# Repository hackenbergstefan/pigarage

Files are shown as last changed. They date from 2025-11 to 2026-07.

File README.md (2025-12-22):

# PiGarage - Smartify your garage gate with license plate recognition

PiGarage controls a gate using a camera, IR sensors, and MQTT. It detects motion, finds license plates, performs OCR, and triggers gate actions based on allowed plates and motion direction.

- [PiGarage - Smartify your garage gate with license plate recognition](#pigarage---smartify-your-garage-gate-with-license-plate-recognition)
  - [Hardware Setup](#hardware-setup)
  - [Software component interaction](#software-component-interaction)
    - [Components](#components)
    - [OcrDetector Preprocessing Steps](#ocrdetector-preprocessing-steps)
  - [Example of image processing pipeline](#example-of-image-processing-pipeline)
  - [Raspberry Pi Shield](#raspberry-pi-shield)
  - [Housing](#housing)

## Hardware Setup

```
___________________________________________________
||          🚥          📷          🔦          ||
||     [Status LED]   [Camera]    [IR Beam]      ||
||                                               ||
||                      📟                       ||
||                 [Raspberry Pi]                ||
||                                         ⛓️    ||
||                                       [Motor] ||
||                                               ||
||                                               ||
||🚧                                          🚧||
||[IR Barrier]                       [IR Barrier]||
||_______________________________________________||
```

Legend:
- 📷 Camera and 🔦 IR Beam mounted at top center above the gate opening.
- 🚧 IR Barrier sensors placed low on left and right sides near the ground.
- 📟 Raspberry Pi
- ⛓️ Motor controlling the gate
- 🚥 Status LED indicating system state

I'm using the following hardware components:
- 📟 Raspberry Pi 4 Model B
- 📷 [IR Camera module](https://www.az-delivery.de/products/raspberry-pi-kamera-nachtsicht-infrarot-kameramodul-5mp-ov5647-webcam)
- 🔦 [IR illuminator](https://www.amazon.de/dp/B09H74YTHN)
- 🚧 [IR Barrier sensors](https://www.amazon.de/dp/B0DY465JHQ)
- 🚥 [Neopixel Ring 12x](https://www.adafruit.com/product/2853)

## Software component interaction

This section illustrates how `LicensePlateProcessor` coordinates the threads `DifferenceDetector`, `PlateDetector`, and `OcrDetector`, including their queue-based communication and pause/resume lifecycle.

```mermaid
sequenceDiagram
    participant LP as LicensePlateProcessor
    participant DD as DifferenceDetector
    participant PD as PlateDetector
    participant OD as OcrDetector

    LP->>DD: resume()
    activate DD
    Note over LP: wait<br> for diff
    DD-->>LP: notify()
    LP->>DD: pause()
    deactivate DD

    LP->>PD: resume()
    activate PD
    Note over PD: Detect plate with YOLO<br/>enqueue plate crop<br/>infer motion direction

    LP->>OD: resume()
    activate OD
    Note over OD: wait()<br> for plate
    OD->>PD: get plate
    Note over OD: Consume plate crop<br/>OCR with EasyOCR

    Note over LP: wait<br> for allowed plate
    OD-->>LP: notify(allowed_plate)
    OD->>OD: pause()
    deactivate OD

    Note over LP: wait<br> for direction
    PD-->>LP: notify(direction)
    PD->>PD: pause()
    deactivate PD

    Note over LP: open/close gate<br>send mqtt message
```

### Components

- **DifferenceDetector**: Captures low-resolution frames, computes MSE, notifies on motion, then pauses.
- **PlateDetector**: Uses YOLO to detect plate crops and infers motion direction from vertical history; publishes to `detected_plates` and `detected_directions`.
- **OcrDetector**: Consumes plate crops, preprocesses and OCRs text; if text matches `allowed_plates`, publishes to `detected_ocrs` and pauses.
- **LicensePlateProcessor**: Orchestrates pause/resume, waits for motion, then concurrently runs plate and OCR; reads `detected_ocrs` and `detected_directions` with timeouts, triggers callbacks.

### OcrDetector Preprocessing Steps

In order to improve OCR accuracy, non-plate areas are masked to focus on text and reduce to black and white.
(See [./src/pi_garage/ocr_detector.py::cv2_mask_non_plate](./src/pi_garage/ocr_detector.py))

## Example of image processing pipeline

1. Original image from camera (from huggingface model page):
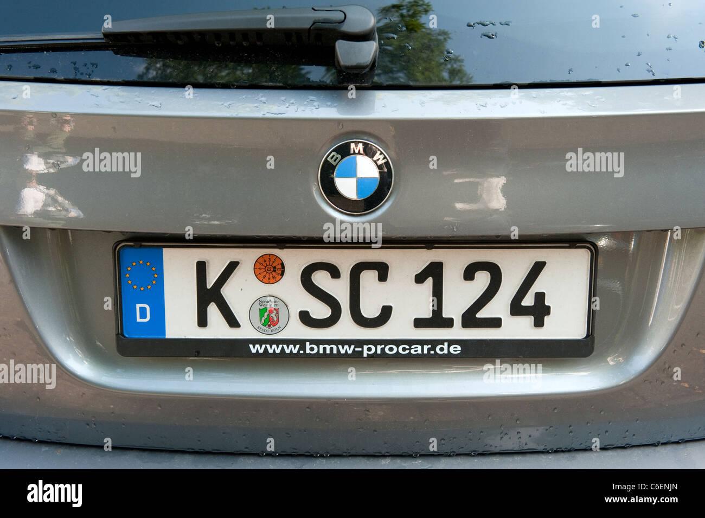
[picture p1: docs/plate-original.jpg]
Original Image
   

2. Detected license plate region (`pigarage-plate-detector ./docs/plate-original.jpg --output ./docs/plate-crop.jpg`):
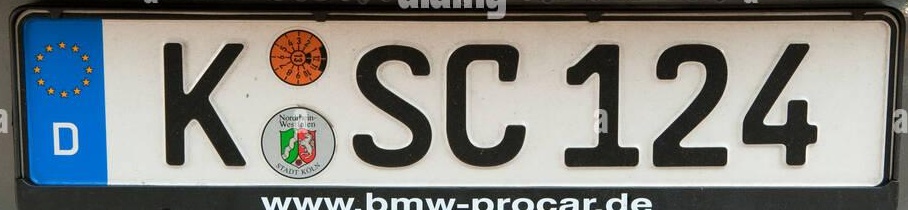
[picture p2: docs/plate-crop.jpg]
Detected Plate
   

3. Masked non-plate areas (`pigarage-ocr-detector improve ./docs/plate-crop.jpg --output ./docs/plate-masked.jpg`):
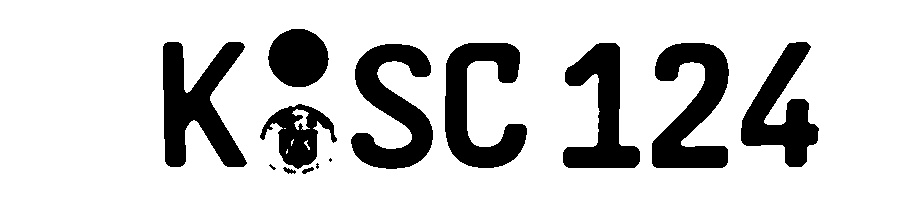
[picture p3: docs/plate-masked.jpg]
Masked Plate
   

4. EasyOCR Result (`pigarage-ocr-detector ocr ./docs/plate-masked.jpg`):
   ```
   K SC 124
   ```

## Raspberry Pi Shield

Wiring diagram for connecting the components to the Raspberry Pi using a custom shield:

Wiring Diagram

See [docs/garage.fzz](docs/garage.fzz) for the Fritzing source file.

## Housing

I designed a custom housing for the camera and the LED ring using Fusion 360.
The source files can be found under [docs/garage-housing.f3d](docs/garage-housing.f3d).
Here are some pictures of the housing:

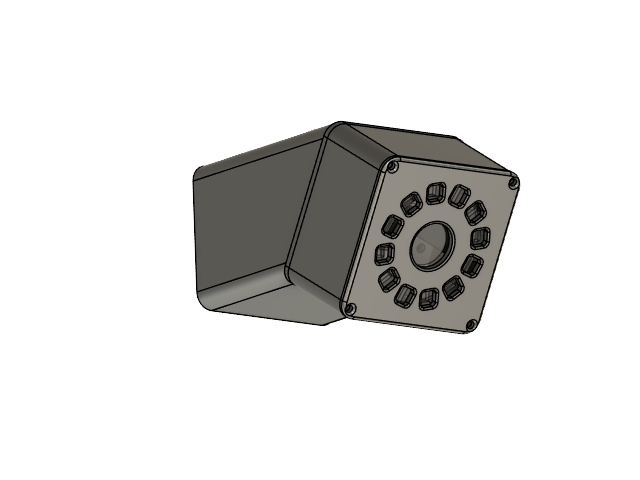
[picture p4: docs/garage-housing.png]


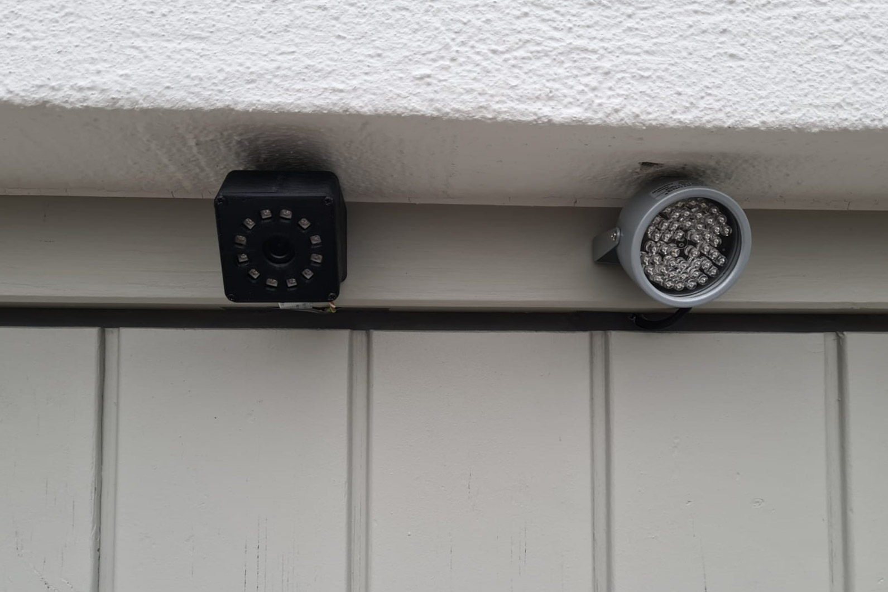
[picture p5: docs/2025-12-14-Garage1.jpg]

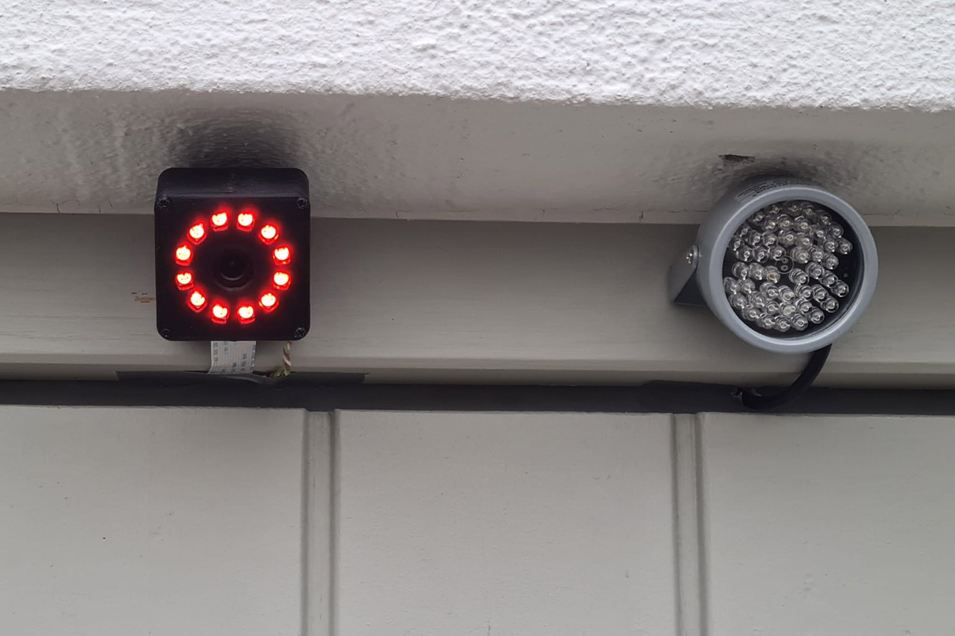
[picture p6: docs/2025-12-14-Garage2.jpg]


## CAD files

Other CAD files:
docs/garage-housing.f3d

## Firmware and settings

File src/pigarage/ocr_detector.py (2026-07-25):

import argparse
import logging
import os
import re
import time
from collections.abc import Callable
from http import HTTPStatus
from http.client import HTTPException
from pathlib import Path
from queue import Queue

os.environ["PADDLE_PDX_ENABLE_MKLDNN_BYDEFAULT"] = "0"

import cv2
import numpy as np
import requests
from paddleocr import PaddleOCR

from .config import VISUAL_DEBUG
from .config import config as pigarage_config
from .util import PausableNotifingThread

TRACE = 5
"""Custom logging level for trace messages."""
logging.addLevelName(TRACE, "TRACE")


def create_ocr() -> PaddleOCR:
    return PaddleOCR(
        lang="en",
        use_doc_orientation_classify=False,
        use_doc_unwarping=False,
        use_textline_orientation=False,
        device="cpu",
        text_rec_score_thresh=0.3,
    )


def cv2_contours_append_children(
    hierarachy: np.ndarray,
    idx: int,
    idxs: set[int],
) -> None:
    if (child := hierarachy[0][idx][2]) != -1:
        idxs.add(child)
        cv2_contours_append_children(hierarachy, child, idxs)
    if (sibling := hierarachy[0][idx][0]) != -1:
        idxs.add(sibling)
        cv2_contours_append_children(hierarachy, sibling, idxs)


def cv2_improve_plate_img(  # noqa: PLR0913
    plate: cv2.typing.MatLike,
    blur: int = 3,
    block_size: int = 181,
    c: float = 2,
    clahe_clip: float = 2.0,
    clahe_tile: int = 5,
    min_plate_area: float = 0.3,
    min_char_height_ratio: float = 0.5,
) -> cv2.typing.MatLike | None:
    plate = cv2.cvtColor(plate, cv2.COLOR_BGR2GRAY) if len(plate.shape) == 3 else plate  # noqa: PLR2004
    plate = cv2.createCLAHE(
        clipLimit=clahe_clip,
        tileGridSize=(clahe_tile, clahe_tile),
    ).apply(plate)
    plate = cv2.resize(plate, None, fx=3, fy=3, interpolation=cv2.INTER_LANCZOS4)

    kernel = np.array([[0, -1, 0], [-1, 5, -1], [0, -1, 0]])
    plate = cv2.filter2D(plate, -1, kernel)

    thresh = cv2.adaptiveThreshold(
        src=cv2.medianBlur(plate, blur),
        maxValue=255,
        adaptiveMethod=cv2.ADAPTIVE_THRESH_GAUSSIAN_C,
        thresholdType=cv2.THRESH_BINARY,
        blockSize=block_size,
        C=c,
    )

    # Calculate contours
    contours, hierarachy = cv2.findContours(
        thresh, cv2.RETR_TREE, cv2.CHAIN_APPROX_SIMPLE
    )
    # Calculate areas of contours and sort them descending
    areas = np.array([cv2.contourArea(c) for c in contours])
    if np.all(areas == 0):
        logging.getLogger(__name__).log(TRACE, "All contours have zero area")
        return None
    idxs = np.argsort(areas)[::-1]
    # Check that plate area is large enough
    if areas[idxs[0]] / (plate.shape[0] * plate.shape[1]) < min_plate_area:
        logging.getLogger(__name__).log(
            TRACE,
            "Plate area too small: %.2e",
            areas[idxs[0]] / (plate.shape[0] * plate.shape[1]),
        )
        return None

    heights = np.array([cv2.boundingRect(c)[3] for c in contours], dtype=np.float32)
    heights /= heights[idxs[0]]

    idxs_to_draw = {i for i in idxs[1:] if heights[i] > min_char_height_ratio}
    if hierarachy.shape[1] > 1000:  # noqa: PLR2004
        logging.getLogger(__name__).log(
            TRACE,
            f"Too many contours ({len(hierarachy)}), skipping child contours",
        )
        return None
    for i in idxs_to_draw.copy():
        cv2_contours_append_children(hierarachy, i, idxs_to_draw)

    masked = cv2.drawContours(
        cv2.bitwise_not(np.zeros(thresh.shape).astype(thresh.dtype)),
        [contours[i] for i in idxs_to_draw],
        -1,
        color=(0, 0, 0),
        thickness=cv2.FILLED,
    )
    # Remove everything outside the largest contour (the plate)
    plate_background = cv2.drawContours(
        np.zeros(thresh.shape).astype(thresh.dtype),
        [contours[idxs[0]]],
        -1,
        color=(255, 255, 255),
        thickness=cv2.FILLED,
    )
    masked = cv2.bitwise_or(masked, cv2.bitwise_not(plate_background))
    if VISUAL_DEBUG:
        cv2.imshow("masked", masked)
        cv2.waitKey(0)
        cv2.destroyAllWindows()
    return masked


def plate2text(plate: cv2.typing.MatLike, ocr: PaddleOCR | None = None) -> str:
    ocr = ocr or create_ocr()
    result = ocr.predict(plate)[0]
    logging.getLogger(__name__).debug(
        f"OCR result: {result['rec_texts']} with {result['rec_scores']}"
    )
    return result["rec_texts"][0]


class OcrDetector(PausableNotifingThread):
    def __init__(  # noqa: PLR0913
        self,
        detected_plates: Queue,
        allowed_plates: list[str],
        ocr_regex: str = r"[A-Z]{1,2}\.? ?\.?[A-Z]{0,2} ?[0-9]{2,4}$",
        on_ocr_detected: Callable[[str], None] = lambda _: None,
        *,
        cv2_improve_plate_img_kwargs: dict | None = None,
        debug: bool = False,
    ) -> None:
        super().__init__()
        self._debug = debug
        self._detected_plates = detected_plates
        self.detected_ocrs = Queue(maxsize=1)
        self._ocr_regex = ocr_regex
        self._ocr = create_ocr()
        self.allowed_plates = allowed_plates
        self._on_ocr_detected = on_ocr_detected
        self._remote_session = requests.Session()
        self._cv2_improve_plate_img_kwargs = cv2_improve_plate_img_kwargs

    def resume(self) -> None:
        while self.detected_ocrs.qsize() > 0:
            self.detected_ocrs.get_nowait()
        return super().resume()

    def _postprocess(self, ocr: str) -> str:
        ocr = re.search(self._ocr_regex, ocr)
        if ocr:
            return ocr.group(0)
        return None

    def _process_remote(self, plate: cv2.typing.MatLike) -> str | None:
        logging.getLogger(__name__).debug("Using remote OCR")
        plate = cv2.cvtColor(plate, cv2.COLOR_BGR2GRAY)
        response = self._remote_session.post(
            f"{pigarage_config.client['url']}/ocr",
            headers={"auth": pigarage_config.client["auth"]},
            data=cv2.imencode(".jpg", plate)[1].tobytes(),
        )
        if response.status_code != HTTPStatus.OK:
            raise HTTPException(f"Remote OCR failed with {response.status_code}")
        return response.json().get("result")

    def _process_local(self, plate: cv2.typing.MatLike) -> str | None:
        logging.getLogger(__name__).debug("Using local OCR")
        plate = cv2_improve_plate_img(
            plate, **(self._cv2_improve_plate_img_kwargs or {})
        )
        if plate is None:
            return None
        if self._debug:
            cv2.imwrite(
                pigarage_config.logdir
                / f"{time.strftime('%Y-%m-%d_%H-%M-%S')}_ocr_post.jpg",
                plate,
            )
        return plate2text(plate, ocr=self._ocr)

    def process(self) -> None:
        plate = self._detected_plates.get()

        if self._debug:
            cv2.imwrite(
                pigarage_config.logdir
                / f"{time.strftime('%Y-%m-%d_%H-%M-%S')}_ocr_pre.jpg",
                plate,
            )

        if "url" in pigarage_config.client:
            try:
                result = self._process_remote(plate)
            except (requests.RequestException, HTTPException) as e:
                logging.getLogger(__name__).warning(
                    f"Remote OCR failed, falling back to local OCR: {e}"
                )
                result = self._process_local(plate)
        else:
            result = self._process_local(plate)

        ocr = self._postprocess(result)
        self._log.info(f"OCR: '{result.strip()}' -> '{ocr}'")
        if ocr is not None:
            self._on_ocr_detected(ocr)
        if ocr is not None and ocr in self.allowed_plates:
            self.detected_ocrs.put(ocr)
            self._notify_waiters()
            self.pause()


def main() -> None:
    logging.basicConfig(level=TRACE)
    parser = argparse.ArgumentParser()
    parser.add_argument(
        "action",
        choices=("improve", "ocr"),
        help="Action to perform",
    )
    parser.add_argument("input", type=Path, help="Path to the image file")
    parser.add_argument(
        "--output",
        type=Path,
        help="Path to save the output image. "
        "If not provided, the image will be shown using cv2.imshow.",
    )
    parser.add_argument(
        "--visual-debug",
        action="store_true",
        help="Enable visual debug mode with additional output.",
    )
    args = parser.parse_args()

    global VISUAL_DEBUG  # noqa: PLW0603
    VISUAL_DEBUG = args.visual_debug
    img = cv2.imread(str(args.input))

    match args.action:
        case "improve":
            out = cv2_improve_plate_img(img)
        case "ocr":
            result = plate2text(img)
            logging.getLogger(__name__).info(f"OCR result: '{result}'")
            return

    if args.output:
        cv2.imwrite(str(args.output), out)
    else:
        cv2.imshow("output", out)
        cv2.waitKey(0)
        cv2.destroyAllWindows()


if __name__ == "__main__":
    main()

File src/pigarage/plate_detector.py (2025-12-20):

import argparse
import logging
import time
from collections.abc import Callable
from dataclasses import dataclass
from pathlib import Path
from queue import Queue

import cv2
import ultralytics
from huggingface_hub import hf_hub_download
from ultralytics import YOLO

try:
    from picamera2 import Picamera2
except ImportError:
    from unittest.mock import MagicMock

    Picamera2 = MagicMock()

from .config import config as pigarage_config
from .util import PausableNotifingThread


def increment_path_exists_ok(
    path: str | Path,
    *,
    exist_ok: bool = False,  # noqa: ARG001
    sep: str = "",  # noqa: ARG001
    mkdir: bool = False,  # noqa: ARG001
) -> Path:
    return path


ultralytics.utils.files.increment_path = increment_path_exists_ok
ultralytics.utils.LOGGER.setLevel(logging.WARNING)


@dataclass
class Box:
    x1: int
    y1: int
    x2: int
    y2: int

    @property
    def center_x(self) -> float:
        return (self.x1 + self.x2) / 2

    @property
    def center_y(self) -> float:
        return (self.y1 + self.y2) / 2


class PlateHistory:
    def __init__(self, different_plate_distance: int) -> None:
        self._boxes: list[Box] = []
        self._different_plate_distance = different_plate_distance

    def get(self, box: Box) -> Box | None:
        """Get existing plate close to center_x, if any."""
        for prev_box in self._boxes:
            if abs(box.center_x - prev_box.center_x) < self._different_plate_distance:
                return prev_box
        return None

    def update_x(self, box: Box) -> None:
        """Update x position of existing plates to account for movement."""
        for prev_box in self._boxes:
            if abs(box.center_x - prev_box.center_x) < self._different_plate_distance:
                prev_box.x1 = box.x1
                prev_box.x2 = box.x2

    def add_or_update(self, box: Box) -> bool:
        """Add new plate position or update existing one."""
        if self.get(box) is not None:
            self.update_x(box)
            return False
        self._boxes.append(box)
        return True

    def clear(self) -> None:
        self._boxes = []


class PlateDetector(PausableNotifingThread):
    def __init__(  # noqa: PLR0913
        self,
        cam: Picamera2,
        cam_setting: str = "main",
        on_resume: Callable[[], None] = lambda: None,
        on_notifying: Callable[[], None] = lambda: None,
        direction_min_distance: int = 50,
        direction_ignore_distance: int = 5,
        different_plate_distance: int = 100,
        *,
        debug: bool = False,
    ) -> None:
        super().__init__(on_resume=on_resume, on_notifying=on_notifying)
        self.model = YOLO(
            hf_hub_download(
                "morsetechlab/yolov11-license-plate-detection",
                "license-plate-finetune-v1n.pt",
            )
        )
        self._cam = cam
        self._cam_setting = cam_setting
        self._debug = debug
        self.detected_plates = Queue(maxsize=0)
        self.detected_directions = Queue(maxsize=0)
        self._direction_min_distance = direction_min_distance
        self._direction_ignore_distance = direction_ignore_distance
        self._different_plate_distance = different_plate_distance
        self._history = PlateHistory(different_plate_distance)

    def resume(self) -> None:
        while self.detected_plates.qsize() > 0:
            self.detected_plates.get_nowait()
        while self.detected_directions.qsize() > 0:
            self.detected_directions.get_nowait()
        self._history.clear()
        return super().resume()

    def _detect_plate_boxes(self, img: cv2.typing.MatLike) -> list[Box]:
        results = self.model.predict(
            source=img,
            verbose=False,
            save=self._debug,
            save_crop=self._debug,
            project="/tmp",  # noqa: S108
            name="plate_detector",
            imgsz=512,
        )
        boxes: list[Box] = []
        # Detect plates
        for box in results[0].boxes:
            x1, y1, x2, y2 = map(int, box.xyxy[0].tolist())
            box = Box(x1, y1, x2, y2)  # noqa: PLW2901
            boxes.append(box)
        return boxes

    def _update_history(self, img: cv2.typing.MatLike, boxes: list[Box]) -> None:
        """Update plate history and notify about new plates."""
        for i, box in enumerate(boxes):
            if self._history.add_or_update(box):
                self._log.debug(
                    f"New plate detected at ({box.center_x}, {box.center_y})"
                )
                if self._debug:
                    cv2.imwrite(
                        pigarage_config.logdir
                        / f"{time.strftime('%Y-%m-%d_%H-%M-%S')}_plate_{i}.jpg",
                        cv2.resize(
                            cv2.rectangle(
                                img,
                                (box.x1, box.y1),
                                (box.x2, box.y2),
                                color=(255, 0, 0),
                                thickness=3,
                            ),
                            dsize=(int(0.2 * img.shape[1]), int(0.2 * img.shape[0])),
                        ),
                    )
                self.detected_plates.put(img[box.y1 : box.y2, box.x1 : box.x2])
                self._notify_waiters()

    def _detect_direction(self, img: cv2.typing.MatLike, boxes: list[Box]) -> None:
        """Detect direction of plates based on y position changes."""
        for box in boxes:
            prev = self._history.get(box)
            if prev is None:
                continue
            if abs(box.center_y - prev.center_y) < self._direction_ignore_distance:
                continue
            self._log.debug(f"Plate updated ({box.center_x}, {box.center_y})")

            self.detected_plates.put(img[box.y1 : box.y2, box.x1 : box.x2])
            self._notify_waiters()

            diff = box.center_y - prev.center_y
            if abs(diff) < self._direction_min_distance:
                return

            direction = "arriving" if diff > 0 else "leaving"
            self._log.debug(f"direction: {direction}")
            self.detected_directions.put(direction)
            self._notify_waiters()

    def process(self) -> None:
        img = self._cam.capture_array(self._cam_setting)
        boxes = self._detect_plate_boxes(img)
        if len(boxes) == 0:
            return
        self._update_history(img, boxes)
        self._detect_direction(img, boxes)
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

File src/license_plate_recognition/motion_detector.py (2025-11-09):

import logging
from typing import Literal

import cv2
import numpy as np
from picamera2 import Picamera2

from .util import DetectionThread


class MotionDetector(DetectionThread):
    def __init__(
        self,
        cam: Picamera2,
        cam_setting="lowres",
        history: int = 50,
        variance_threshold: int = 80,
        resize: int = 480,
        *,
        debug: bool = False,
    ):
        super().__init__(cam=cam, cam_setting=cam_setting)

        self.tracker = cv2.createBackgroundSubtractorMOG2(
            history=history,
            detectShadows=False,
            varThreshold=variance_threshold,
        )
        self.history = []
        self.history_length = 6
        self.resize = resize
        self.debug = debug

    def _center_of_mass(self, img: cv2.typing.MatLike) -> float | None:
        """
        Calculate y-coordinate of center of mass of the convex hull of all contours in the image.
        """
        # Find contours in the image
        contours, _ = cv2.findContours(img, cv2.RETR_EXTERNAL, cv2.CHAIN_APPROX_SIMPLE)
        if not contours:
            return None

        # Calculate the convex hull of the contours
        hull = cv2.convexHull(np.vstack(contours))

        # Calculate the center of mass of the convex hull
        moments = cv2.moments(hull)
        if moments["m00"] == 0:
            return None
        center_x = int(moments["m10"] / moments["m00"])
        center_y = int(moments["m01"] / moments["m00"])

        if self.debug:
            # Draw the convex hull and center of mass on the image for debugging
            img = cv2.cvtColor(img, cv2.COLOR_GRAY2BGR)
            img = cv2.drawContours(img, [hull], -1, color=(255, 0, 0), thickness=3)
            img = cv2.circle(
                img,
                (center_x, center_y),
                radius=7,
                color=(0, 0, 255),
                thickness=-1,
            )
            cv2.imwrite("/tmp/motion_detector.jpg", img)
        return center_y

    def process(self, img: cv2.typing.MatLike) -> None | Literal["arriving", "leaving"]:
        """
        Process the image to detect motion direction based on the center of mass of the convex hull
        of the contours in the foreground mask.
        """
        # img = cv2.resize(
        #     img,
        #     dsize=(self.resize, int(img.shape[0] / img.shape[1] * self.resize)),
        # )
        fg_mask = self.tracker.apply(img)
        center_y = self._center_of_mass(fg_mask)
        if center_y is not None:
            self.history.append(center_y)

        # Detect motion direction based on the history of center of mass positions
        if len(self.history) == self.history_length:
            ys = sorted(range(self.history_length), key=lambda i: self.history[i])
            logging.getLogger(__name__).debug(f"ys: {ys}")
            self.history.clear()
            if ys == list(range(self.history_length)) and ys[0] != ys[-1]:
                direction = "arriving"
                logging.getLogger(__name__).debug(f"direction: {direction}")
                return direction
            if ys == list(reversed(range(self.history_length))) and ys[0] != ys[-1]:
                direction = "leaving"
                logging.getLogger(__name__).debug(f"direction: {direction}")
                return direction
        return None

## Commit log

2025-11-27 Improve masking of plate
2025-12-12 Rework threads
2025-12-13 Improve plate detector algorithm
2025-12-14 Add README and fix tests
    [garage-housing.f3d, garage.fzz]
2025-12-20 Fix mean squared error calculation in diff_detector
    [diff_detector.py]
2025-12-20 Improve plate detection to support multiple plates
2025-12-20 Save only new plate images
2025-12-20 Resize plate detector image before saving
2025-12-20 Fix during live test
    [ocr_detector.py, plate_detector.py]
2025-12-22 Improve plate image masking to better isolate plate area
2025-12-22 Fix tests and tweak plate improving
    [ocr_detector.py]
